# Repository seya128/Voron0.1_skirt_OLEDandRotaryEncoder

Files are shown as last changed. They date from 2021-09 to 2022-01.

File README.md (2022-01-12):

# Voron0.1_skirt_OLEDandRotaryEncoder

Voron0.1: 0.96インチOLE&ロータリーエンコーダーをスカートに内蔵

OLEDとロータリエンコーダーは、MCUボードを経由せずにRaspberryPiに直接配線するので、MCUボードの種類に関係なく設定できます。  
なので、Voron0.1以外でもKlipperで動作する3Dプリンターに応用できます。

## 完成形









## 部品

- 0.96インチOLED

    [https://amzn.to/3zsqpv](https://amzn.to/3zsqpv2)

- ロータリーエンコーダー

    [https://amzn.to/3hOiPFf](https://amzn.to/3hOiPFf)

    ３つのスイッチ全てにプルアップ抵抗がついてるもの

- M2 x 4mm タッピングビス ４本

## 配線図

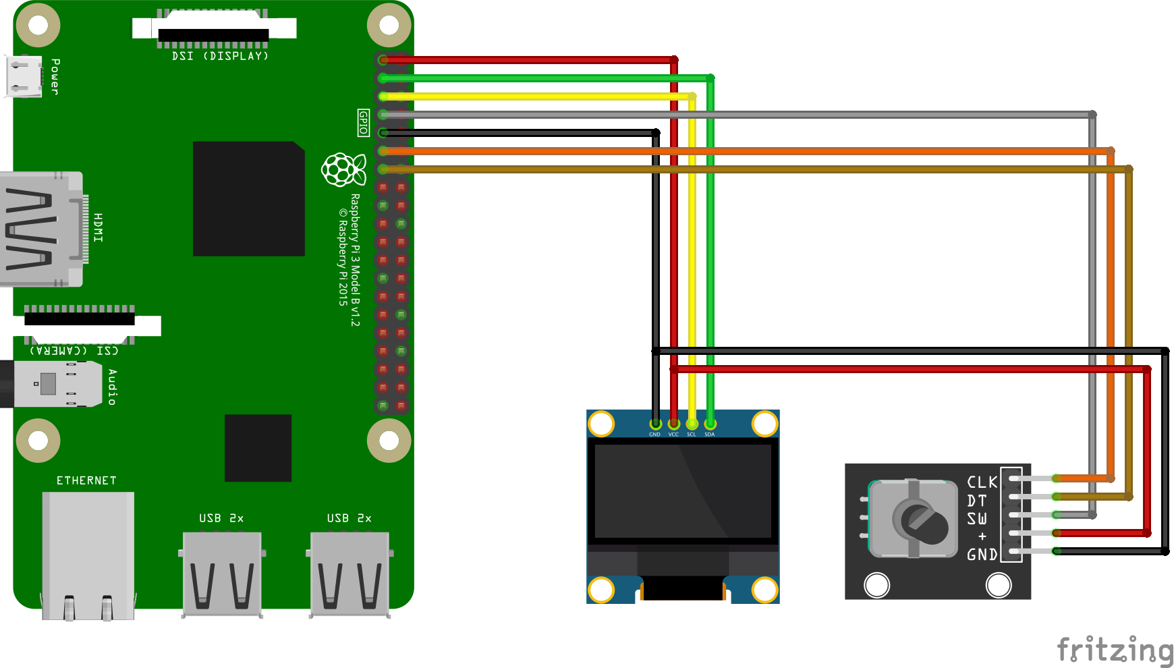
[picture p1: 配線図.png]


rpi:3.3v —- OLED:VCC, RENC:+

rpi:GPIO2(SDA1) —- OLED:SDA 

rpi:GPIO3(SCL1) —- OLED:SCL

rpi:GPIO4 —- RENC:SW

rpi:GND —- OLED:GND, RENC:GND

rpi:GPIO17 —- RENC:CLK

rpi:GPIO27 —- RENC:DT

## ケーブル作成

ケーブル長は、75cmぐらい。

### VCCとGNDを二股にする

追加するケーブルは、ながさ12cmぐらい。

途中の被覆を剥いて、そこに追加の配線を巻いてハンダ。





そして、熱収縮チューブを被せる。



QIコネクタを取り付け



### OLEDのピンを曲げる

取り付けた時にコネクタが電源ユニットに当たるので、当たらないようにコネクタに角度をつけるためピンを曲げる。

スカートの厚さからコネクタが出ないくらいに曲げる。



### スカートにOLEDを取り付け

M2x4mmのタッピングビス４本で取り付け。



### スカートにロータリーエンコーダ取り付け

付属のナットで取り付け。



## configファイル

```
[mcu rpi]
serial: /tmp/klipper_host_mcu

[display]
lcd_type: ssd1306
i2c_mcu: rpi
i2c_bus: i2c.1
i2c_address: 60 #(0x3c) 
encoder_pins: rpi:gpio17, rpi:gpio27
click_pin: !rpi:gpio4
```

※以下の手順でセカンダリーMCUとしてRaspberryPiを指定できるようにしておく必要があります。  
[RPi microcontroller \- Klipper documentation](https://www.klipper3d.org/RPi_microcontroller.html)

※`sudo raspi-config` - [インターフェイスオプション]メニューで`i2c`を有効にする必要もあります。

## 元にしたSTLデータ

* [VoronUsers/printer_mods/mpfl/V0.1_skirt_OLED at master · VoronDesign/VoronUsers](https://github.com/VoronDesign/VoronUsers/tree/master/printer_mods/mpfl/V0.1_skirt_OLED)

* [Customizable Knob! by charliearmorycom](https://www.thingiverse.com/thing:54024)

## ちょっと便利なメニュー

### BED SCREW ADJUST
BEDのレベル調整に使う、「BED_SCREW_ADJUST」をメニューから使う設定です。
`Home All` `Adjusted` `Abort` が、コンソールからでなく、メニューから操作できるのでとっても便利。

menu.cfg に以下追加で、Setup-Calibrationに追加されます。
```
[menu __main __setup __calib]
type: list
name: Calibration

[menu __main __setup __calib __bed_screw_adjust]
type: list
enable: {not printer.idle_timeout.state == "Printing"}
name: Bed Screw Adjust
index: 1

[menu __main __setup __calib __bed_screw_adjust __home]
type: command
enable: {not printer.idle_timeout.state == "Printing"}
name: Home All
gcode: G28

[menu __main __setup __calib __bed_screw_adjust __start]
type: command
enable: {not printer.idle_timeout.state == "Printing"}
name: Start BedScrewAdjust
gcode:
    BED_SCREWS_ADJUST

[menu __main __setup __calib __bed_screw_adjust __adjusted]
type: command
name: Adjusted
gcode:
    ADJUSTED

[menu __main __setup __calib __bed_screw_adjust __abort]
type: command
name: Abort
gcode:
    ABORT
```

## 投げ銭

[Amazonギフト券](https://amzn.to/39yuS50)  
受取人に、 `giftforseya+v01OLED@gmail.com`を入れてください。  
15円から投げ銭可能ですので、気に入ったらよろしくお願いします。

## キット、パーツ販売
キットやパーツの販売も始めました。
https://seya-factory.booth.pm/items/3550556

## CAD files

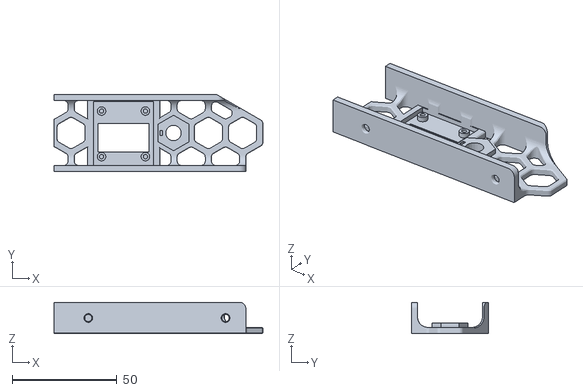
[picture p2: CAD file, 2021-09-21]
v0.1-skirt-oled_rotaryencoder.stl
100.0 x 37.0 x 15.0

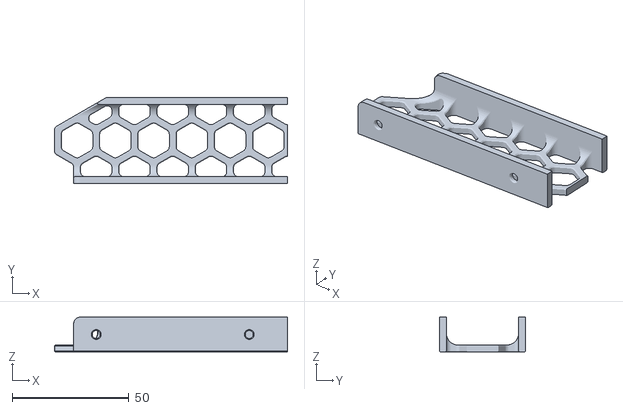
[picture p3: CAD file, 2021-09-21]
Skirt_x3.STL
100.0 x 37.0 x 15.0

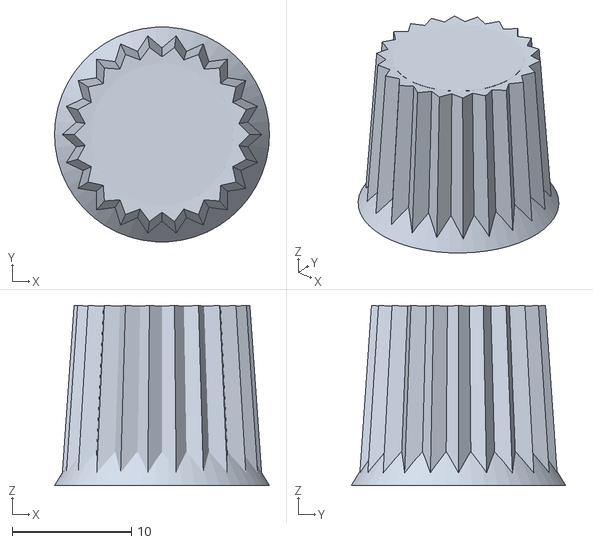
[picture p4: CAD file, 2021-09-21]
CustomizableKnob_v0_renc.stl
18.0 x 18.0 x 15.1

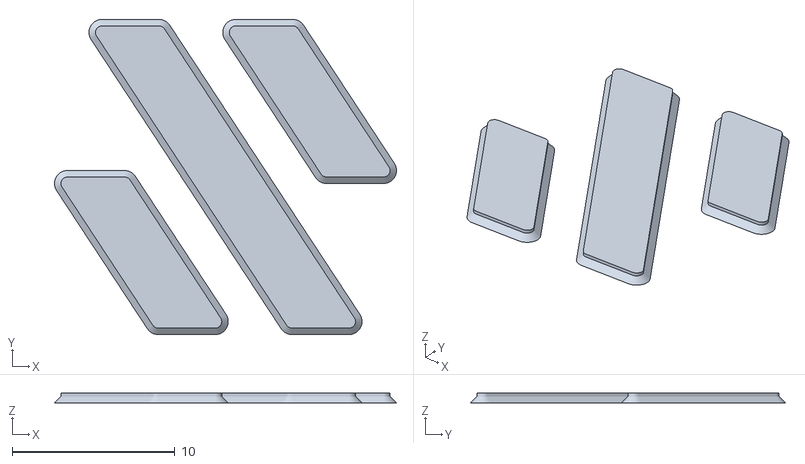
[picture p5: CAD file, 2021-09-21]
Cowling_LOGO_ONLY_x1.STL
21.0 x 19.4 x 0.6

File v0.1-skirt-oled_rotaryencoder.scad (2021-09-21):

bezel = 0.4;
bezel_h = calculate_bezel(bezel);
screen_bezel = 3.6;
screen_bezel_h = calculate_bezel(screen_bezel);
prototype = false;

standoff_screw_diameter = 2.1;
standoff_outer_diameter = standoff_screw_diameter + 2;


OLED_HOLE_SPACE_W = 21.0; 
OLED_HOLE_SPACE_H = 21.8;

OLED_X = (27.5+5+2)/2;

OFS_X = 16;

/*
translate([0,0, bezel+2.6])
    oled_proxy();
difference() {
    translate([0, 0, bezel])
        oled_holder_positive();
    translate([0,0, 2])
        oled_holder_negative();
}
*/

// rotary_encoder_holder();

/*
translate([OLED_X,(27.8+6+2-bezel)/2 +0.5, bezel+2.6])
        oled_proxy();
*/

difference() {
    union() {
        stock_skirt();
        translate([OFS_X,0,0,]) {
            translate([OLED_X, (27.8+6+2-bezel)/2 +0.5, bezel])
                oled_holder_positive();
            translate([41.2,18.5, 0])
                rotary_encoder_holder();
        }    
    }
    translate([OFS_X,0,0]) {
        translate([OLED_X, 2.6+31/2, 2])
            oled_holder_negative();
        if (prototype) {
            translate([OLED_X+35, -10, -10])
                cube([100,70,50]); 
            mirror([1,0,0])
            translate([OLED_X+25, -10, -10])
                cube([100,50,50]);
        }
        translate([OLED_X-30,1,-0.01])
            scale([0.5, 0.5, 1])
                import("Cowling_LOGO_ONLY_x1.STL");
    }
}

module stock_skirt() {
//    translate([-110,-41.5,0])
//        import("Skirt_x3.STL");

    mirror([1,0,0])
        translate([-110,-41.5,0])
            import("Skirt_x3.STL");
}

module rotary_encoder_holder() {

    difference() {
        
        // 六角柱
        order = 6;
        r=17/2;
        angles=[ for (i = [0:order-1]) i*(360/order) ];
        coords=[ for (th=angles) [r*cos(th), r*sin(th)] ];
        linear_extrude(height=5.0)
            rotate([0,0,30])
            color("blue")
            polygon(coords);

        // 穴
        cylinder(h=6, r=7.4/2, $fn=20);
        
        // 切り欠き
        translate([-6,0,5.0])
            cube([0.6*2,2.4,2.0*2], center=true);
    }
    
}


module oled_proxy() {
    
    translate([-OLED_HOLE_SPACE_W/2-2,-OLED_HOLE_SPACE_H/2-2,0]) {
        
        translate([0.5,4.0,-2])
            color("black")
                cube([24,13.5,2]);
        difference() {
            color("green")
                cube([OLED_HOLE_SPACE_W+2*2, OLED_HOLE_SPACE_H+2*2, 1.6]);
            translate([2,2,-0.4])
                cylinder(d = standoff_screw_diameter, h=2, $fn=30);
            translate([2,2+OLED_HOLE_SPACE_H,-0.4])
                cylinder(d = standoff_screw_diameter, h=2, $fn=30);
            translate([2+OLED_HOLE_SPACE_W,2+OLED_HOLE_SPACE_H,-0.4])
                cylinder(d = standoff_screw_diameter, h=2, $fn=30);
            translate([2+OLED_HOLE_SPACE_W,2,-0.4])
                cylinder(d = standoff_screw_diameter, h=2, $fn=30);

        }
    }
}

module oled_holder_positive() {
    translate([-(27.5+5+2)/2, -(27.8+6+2)/2,0]) {
        minkowski() {
            cube([27.5+5+2-bezel_h, 27.8+6+2-bezel, 3-2*bezel]);
            rotate([0,45,0])
                cube([bezel_h,bezel_h,bezel_h]);
        }
    }
    translate([-OLED_HOLE_SPACE_W/2,-OLED_HOLE_SPACE_H/2,2])
        screen_standoff();
    translate([-OLED_HOLE_SPACE_W/2,+OLED_HOLE_SPACE_H/2,2])
        screen_standoff();
    translate([+OLED_HOLE_SPACE_W/2,-OLED_HOLE_SPACE_H/2,2])
        screen_standoff();
    translate([+OLED_HOLE_SPACE_W/2,+OLED_HOLE_SPACE_H/2,2])
        screen_standoff();
}

module oled_holder_negative() {
    difference() {
        union() {
            translate([-28.5/2,-31/2,-1])
            cube([28.5, 31, 10]); // PCB cutout
            translate([-OLED_HOLE_SPACE_W/2,-OLED_HOLE_SPACE_H/2,-1])
                cylinder(d = standoff_screw_diameter, h = 4, $fn = 30);
            translate([-OLED_HOLE_SPACE_W/2,OLED_HOLE_SPACE_H/2,-1])
                cylinder(d = standoff_screw_diameter, h = 4, $fn = 30);
            translate([OLED_HOLE_SPACE_W/2,-OLED_HOLE_SPACE_H/2,-1])
                cylinder(d = standoff_screw_diameter, h = 4, $fn = 30);
            translate([OLED_HOLE_SPACE_W/2,OLED_HOLE_SPACE_H/2,-1])
                cylinder(d = standoff_screw_diameter, h = 4, $fn = 30);
        }
        translate([-OLED_HOLE_SPACE_W/2,-OLED_HOLE_SPACE_H/2,-2])
            screen_standoff();
        translate([-OLED_HOLE_SPACE_W/2,OLED_HOLE_SPACE_H/2,-2])
            screen_standoff();
        translate([OLED_HOLE_SPACE_W/2,-OLED_HOLE_SPACE_H/2,-2])
            screen_standoff();
        translate([OLED_HOLE_SPACE_W/2,OLED_HOLE_SPACE_H/2,-2])
            screen_standoff();
    }
    // Screen cutout
    translate([-28.5/2,-31/2-0.2,0]) {
        translate([4.5/2-screen_bezel,7.1,-12]) {
            minkowski() {
                cube([24-screen_bezel_h,13.5-screen_bezel_h,0.3]);
                minkowski() {
                rotate([0,45,0])
                    cube(screen_bezel_h);
                rotate([45,0,0])
                    cube(screen_bezel_h);
                }
            }
        }
    }
}

module screen_standoff() {
    difference() {
        cylinder(d = standoff_outer_diameter, h = 3, $fn = 30);
        cylinder(d = standoff_screw_diameter, h = 4, $fn = 30);
    }
}

function calculate_bezel(bezel) = ((bezel*bezel)*2)^0.5;

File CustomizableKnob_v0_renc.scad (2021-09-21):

//////////////////////////
// Customizable settings
//////////////////////////


// Diameter of the hole on the bottom (in mm).
// 底面の穴の直径（単位：mm）
HoleDiameter = 6.0 + 0.3;

// Depth of the hole in the bottom (in mm).  If you want the hole to go all the way through then set this to a number larger than the total height of the object.
// 底面に開ける穴の深さ（単位：mm）。 穴を完全に貫通させたい場合は、オブジェクトの全高よりも大きな数値を設定してください。
HoleDepth = 14;

// If you want a D-shaped hole, set this to the thickness of the flat side (in mm).  Larger values for the flat make the hole smaller.
// D型の穴にしたい場合は、平らな面の厚さ（単位：mm）を設定してください。 平面の値を大きくすると、穴が小さくなります。
HoleFlatThickness = 1.0;

Hole2Diameter = 7.5;
Hole2Depth = 4;

Hole3Diameter = 12.5;
Hole3Depth = 3;


// Height (in mm).  If dome cap is selected, it is not included in height.  The shaft length is also not counted.
// 高さ（単位：mm）。 ドームキャップを選択した場合、高さには含まれません。 シャフトの長さもカウントされません。
KnobHeight = 15;

// Diameter of base of round part of knob (in mm).  (Knurled ridges are not included in this measurement.)
// ノブの丸い部分の底面の直径（単位：mm）。 (ローレットの稜線はこの測定に含まれません）
KnobDiameter = 14;

// Shape of top of knob.  "Recessed" type can be painted.
// ノブの上部の形状。 「埋め込みタイプは塗装が可能です。
CapType = 0;	// [0:Flat, 1:Recessed, 2:Dome]

// Do you want a large timer-knob style pointer?
// タイマーノブのような大きなポインターが欲しい？
TimerKnob= 0;	// [0:No, 1:Yes]

// Would you like a divot on the top to indicate direction?
// トップに方向性を示すディボットを入れますか？
Pointer1 = 0;	// [0:No, 1:Yes]

// Would you like a line (pointer) on the front to indicate direction?
// フロントに方向を示すライン（ポインター）が欲しいですか？
Pointer2 = 0;	// [0:No, 1:Yes]

// Do you want finger ridges around the knob?
// ノブの周りに指の隆起が必要ですか？
Knurled = 1;	// [0:No, 1:Yes]

// 0 = A cylindrical knob, any other value will taper the knob.
// 0 = 円筒形のノブ、それ以外の値ではノブが細くなります。
TaperPercentage = 15;		// [0:0%, 10:10%, 20:20%, 30:30%, 40:40%, 50:50%]

// Width of "dial" ring (in mm).  Set to zero if you don't want the ring.
// ダイヤル "リングの幅（単位：mm）。 リングが不要な場合はゼロに設定してください。
RingWidth = 2;

// The number of markings on the dial.  Set to zero if you don't want markings.  (RingWidth must be non-zero.)
// ダイヤル上のマーキングの数。 マークを付けたくない場合はゼロに設定します。 (RingWidthは0以外でなければならない)
RingMarkings = 0;

// diameter of the hole for the setscrew (in mm).  If you don't need a hole, set this to zero.
// 止めねじの穴の直径（単位：mm）。 穴が必要ない場合は、0に設定してください。
ScrewHoleDiameter = 0;

// Length of the shaft on the bottom of the knob (in mm).  If you don't want a shaft, set this value to zero.
// ノブの底面にあるシャフトの長さ（単位：mm）。 シャフトが不要な場合は、この値をゼロにしてください。
ShaftLength = 0;

// Diameter of the shaft on the bottom of the knob (in mm).  (ShaftLength must be non-zero.)
// ノブの下部にあるシャフトの直径（単位：mm）。 (ShaftLengthは0以外でなければなりません)
ShaftDiameter = 10;

// Would you like a notch in the shaft?  It can be used for a press-on type knob (rather than using a setscrew).  (ShaftLength must be non-zero.)
// 軸に切り込みを入れますか？ プレスオンタイプのノブに使用できます（止めねじを使用するのではなく）。 (ShaftLengthは0以外でなければなりません。)
NotchedShaft = 0;	// [0:No, 1:Yes]



//////////////////////////
//Advanced settings
//////////////////////////

RingThickness = 5*1;
DivotDepth = 1.5*1;
MarkingWidth = 1.5*1;
DistanceBetweenKnurls = 2*1;
TimerKnobConst = 1.8*1;



//////////////////////////
//Calculations
//////////////////////////

PI=3.14159265*1;
KnobMajorRadius = KnobDiameter/2;
KnobMinorRadius = KnobDiameter/2 * (1 - TaperPercentage/100);
KnobRadius = KnobMinorRadius + (KnobMajorRadius-KnobMinorRadius)/2;
KnobCircumference = PI*KnobDiameter;
Knurls = round(KnobCircumference/DistanceBetweenKnurls);
Divot=CapType;

TaperAngle=asin(KnobHeight / (sqrt(pow(KnobHeight, 2) +
		pow(KnobMajorRadius-KnobMinorRadius,2)))) - 90;

DivotRadius = KnobMinorRadius*.4;


union()
{
translate([0, 0, (ShaftLength==0)? 0 : ShaftLength-0.001])
difference()
{
union()
{
	// Primary knob cylinder
	cylinder(h=KnobHeight, r1=KnobMajorRadius, r2=KnobMinorRadius,
			$fn=50);
	
	if (Knurled)
		for (i=[0 : Knurls-1])
			rotate([0, 0, i * (360/Knurls)])
				translate([KnobRadius, 0, KnobHeight/2])
					rotate([0, TaperAngle, 0]) rotate([0, 0, 45])
						cube([2, 2, KnobHeight+.001], center=true);

 	if (RingMarkings>0)
		for (i=[0 : RingMarkings-1])
			rotate([0, 0, i * (360/RingMarkings)])
				translate([KnobMajorRadius + RingWidth/2, 0, 1])
					cube([RingWidth*.5, MarkingWidth, 2], center=true);		
	
	if (Pointer2==1)
		translate([KnobRadius, 0, KnobHeight/2-2])
			rotate([0, TaperAngle, 0])
                translate([-9/2, -3/2, -6])
				cube([9, 3, 8], center=false);		

	if (RingWidth>0)
		translate([0, 0, RingThickness/2])
			cylinder(r1=KnobMajorRadius + RingWidth, r2=KnobMinorRadius,
					h=RingThickness, $fn=50, center=true);

	if (Divot==2)
		translate([0, 0, KnobHeight])
			difference()
			{
				scale([1, 1, 0.5])
					sphere(r=KnobMinorRadius, $fn=50, center=true);

				translate([0, 0, 0-(KnobMinorRadius+.001)])
					cube([KnobMinorRadius*2.5, KnobMinorRadius*2.5,
							KnobMinorRadius*2], center=true);
			}

	if (TimerKnob==1) intersection()
		{
			translate([0, 0, 0-(KnobDiameter*TimerKnobConst) + KnobHeight])
			sphere(r=KnobDiameter*TimerKnobConst, $fn=50, center=true);		
	
			translate([0-(KnobDiameter*TimerKnobConst)*0.1, 0,
					KnobHeight/2])
				scale([1, 0.5, 1])
					cylinder(h=KnobHeight, r=(KnobDiameter*TimerKnobConst) *
							0.8, $fn=3, center=true);
		}
}

// Pointer1: Offset hemispherical divot
if (Pointer1==1)
	translate([KnobMinorRadius*.55, 0, KnobHeight + DivotRadius*.6])
		sphere(r=DivotRadius, $fn=40);

// Divot1: Centered cylynrical divot
if (Divot==1)
	translate([0, 0, KnobHeight])
		cylinder(h=DivotDepth*2, r=KnobMinorRadius-1.5, $fn=50,
				center=true);

if (ShaftLength==0)
{
	// Hole for shaft
	translate([0, 0, HoleDepth/2 - 0.001])
		difference()
		{
			cylinder(r=HoleDiameter/2, h=HoleDepth, $fn=50,
					center=true);
	
			// Flat for D-shaped hole
			translate([(0-HoleDiameter)+HoleFlatThickness, 0, 0])
				cube([HoleDiameter, HoleDiameter, HoleDepth+.001],
						center=true);
		}
        // Hole2
        if (Hole2Depth > 0) {
            translate([0, 0, Hole2Depth/2 - 0.001])
                cylinder(r=Hole2Diameter/2, h=Hole2Depth, $fn=20, center=true);
        }
        // Hole3
        if (Hole3Depth > 0) {
            translate([0, 0, Hole3Depth/2 - 0.001])
                cylinder(r=Hole3Diameter/2, h=Hole3Depth, $fn=20, center=true);
        }
	
	// Hole for setscrew
	if (ScrewHoleDiameter>0)
		translate([0 - (KnobMajorRadius+RingWidth+1)/2, 0,
				HoleDepth/2])
			rotate([0, 90, 0])
			cylinder(h=(KnobMajorRadius+RingWidth+1),
					r=ScrewHoleDiameter/2, $fn=20, center=true);
}

// Make sure bottom ends at z=0
translate([0, 0, -10])
	cube([(KnobMajorRadius+RingWidth) * 4,
			(KnobMajorRadius+RingWidth) * 4, 20], center=true);
}

if (ShaftLength>0)
	difference()
	{
		translate([0, 0, ShaftLength/2])
			cylinder(h=ShaftLength, r=ShaftDiameter/2, $fn=20,
					center=true);

		if (NotchedShaft==1)
		{
			cube([HoleDiameter/2, ShaftDiameter*2, ShaftLength],
					center=true);
		}

		// Hole for shaft
		translate([0, 0, HoleDepth/2 - 0.001])
			difference()
			{
				cylinder(r=HoleDiameter/2, h=HoleDepth, $fn=20,
						center=true);
		
				// Flat for D-shaped hole
				translate([(0-HoleDiameter)+HoleFlatThickness, 0, 0])
					cube([HoleDiameter, HoleDiameter, HoleDepth+.001],
							center=true);
			}
		            
        
		// Hole for setscrew
		if (ScrewHoleDiameter>0)
			translate([0 - (KnobMajorRadius+RingWidth+1)/2, 0,
					HoleDepth/2])
				rotate([0, 90, 0])
				cylinder(h=(KnobMajorRadius+RingWidth+1),
						r=ScrewHoleDiameter/2, $fn=20, center=true);
	}
}

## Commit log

2021-09-21 1stコミット
    [Cowling_LOGO_ONLY_x1.STL, CustomizableKnob_v0_renc.scad, CustomizableKnob_v0_renc.stl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]
2021-09-21 README追加
2021-09-21 完成形の写真を一つ追加
2021-09-21 裏側の写真も追加
2021-09-25 READMEに投げ銭追加
2021-10-08 セカンダリMCUの説明を追加
2021-10-08 i2c設定の説明も追加
2022-01-12 readmeに、BED SCREW ADJUSTのmenu.cfg追加
2022-01-12 キット、パーツ販売のリンク追加
